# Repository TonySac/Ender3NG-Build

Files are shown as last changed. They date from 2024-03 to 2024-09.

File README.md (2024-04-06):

# The Maker Medic's Ender 3 NG Documentation

Visit my [documentation/log page](https://e3nglog.themakermedic.com).

<b>OR</b>

Check out my main [website](https://themakermedic.com).

<small>

This repo was generated using the [just-the-docs template](https://github.com/just-the-docs/just-the-docs-template).

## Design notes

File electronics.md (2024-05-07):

---
title: Electronics
layout: default
nav_order: 6
has_children: true
posted: 2024-04-17
updated: 2024-04-30
---

# Electronics
{: .no_toc }

<details closed markdown="block">
  <summary>
    Table of contents
  </summary>
  {: .text-delta }
1. TOC
{:toc}
</details>

---

The official documentation does not include information on wiring or installing electronics. The following pages cover the electronics and wiring of my personal E3NG. It should not be considered a standard. It is provided for personal reference and inspiration only.

In addition to the standard printer electronics (steppers, thermistors, & heaters) my build makes use of the following specific components:

* BTT SKR Mini E3 V3 Mainboard
* Raspberry Pi 3A+
* SN65HVD230 CAN Tranciver
* BTT EBB36 CAN Toolhead Board
* LEDs

{: .note }
:pencil2: I later upgraded to a Pi 4 that I had laying around. I ran into some bottlenecks with dev environments on the Pi 3A. The 3A should be fine for just a printer.

# Wiring Guidance

{: .warn }
:warning: Incorrectly wiring components can cause damage and/or personal injury.

Wires should be routed in a clean manner. This means out of the way of motion components and not pinched, kinked, or otherwise damaged. Always use the correct wire gauge. Securely crimp all connections and use electrical tape and/or heat shrink to prevent shorting. Standard color conventions are especially important for power wires. Label wires as needed.

I provided a table below of the wire gauges I used for various components on the build. Remember, the bigger AWG number, the smaller the wire.

| Component | AWG |
|---|---|
| AC Power | 16-18 |
| DC Power | 18 |
| Heaters | 18-20 |
| Thermistors | 22 |
| Fans | 22 |
| Steppers | 22 |
| Bed Probe | 22-24 |
| CANbus Comms. | 22 |

# Main Electronics

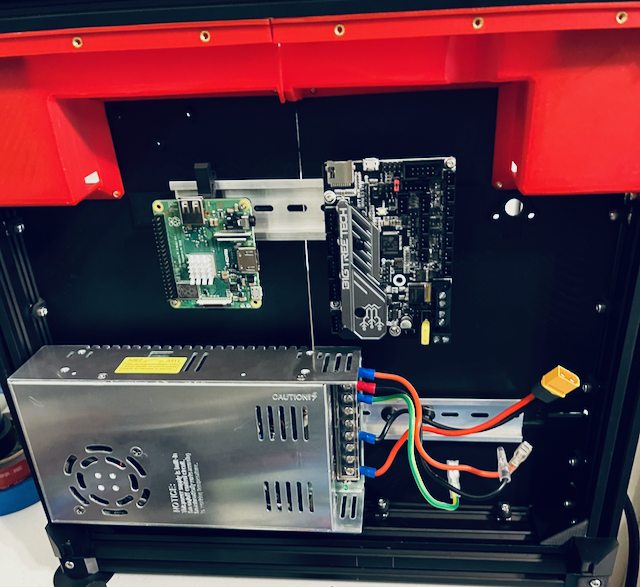
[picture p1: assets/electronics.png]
{: .float-right}{: .ml-3}

I don't feel like there is any "right" way to mount the electronics in the rear of the printer. I used a combination of the included DIN clips and some leftover clips from my Voron build.

The large power supply only fit on the lower DIN rail. I was unsuccessful using `PSU3` and ended up using the standard `DIN1` clip with enlarged holes. In the future I would like to add a buck converter to this lower rail to power the Raspberry Pi. I also need to figure out a more stable way to secure the DIN rail itself.

The upper DIN rail is home to the Raspberry Pi, mainboard, and a CAN transceiver.  I used the DIN clips and brackets from my Voron build, simply because they were already printed and on hand.

For the time being, I do not have an enclosure on the rear of the printer. I would like to clean up the wiring and either print or cut a nice panel to cover the back.

# Toolhead Electronics

{: .mod }
:wrench: Instead of Klicky, I'm reusing the CR Touch.

As previously mentioned, I'm running a Voron Stealthburner for the toolhead. In addition to the usual components (fans, thermistor, and heater) it has some LEDs. I'm also running a BTT EBB36 toolhead board via CANbus. Eventually I will upgrade the CR Touch to a better bed probe and maybe even change the toolhead. 

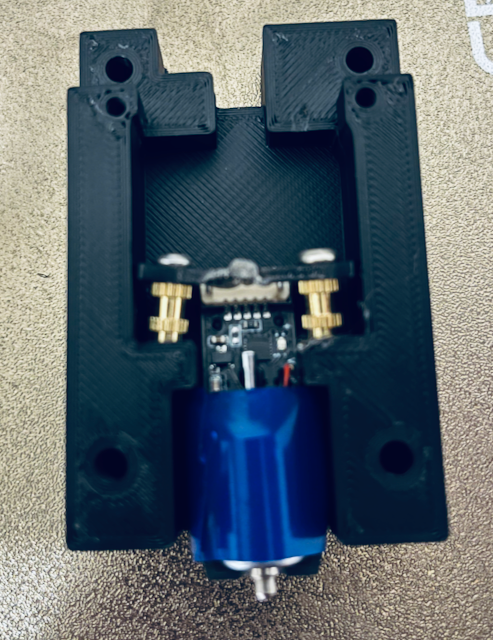
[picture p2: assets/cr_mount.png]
{: .float-right}{: .ml-3}

I made some modification to the CR Touch housing and used [this](https://www.printables.com/model/709806-ender-3-ng-vocano-voron-bltouch-stealthburner) mount to attach the Stealthburner to my E3NG. The mount was originally designed for a BL Touch so I needed to shave down and remove some of the CR Touch housing. I also had to add some spacers to the mount.

>A more elegant solution would be to redesign a mount that fits the probe correctly. With my currently subpar CAD skills and plans to upgrade the probe, I went with my modification instead. 

The big thing to remember with toolhead electronics is to route the wiring an a way that it does not jam up any motion components. The EBB36 CANbus toolhead board helps in this regard. I used one of the many EBB36 mounts found online for the Stealthburner/Clockwork2 then routed and secured loose wires with zip ties.

# Bed Electronics

I reused the stock Ender 3 bed including heater and thermistor. This just required routing the existing cables. Future plans include adding some sort of quick disconnect, maybe WAGOs, to make the bed easier to remove along with a cable chain.

# Switches and LEDs

The Y endstop switch gets mounted on the A motor mount. Originally I planned to use sensorless homing and still will for the X axis. However I had some issues with the calibarating sensorles homing on the Y So I returned to a standard switch. Keeping with the E3NG spirit, I reused an Ender 3 switch and some wiring. I cut the endstop out of the old mounting board and used some DuPont connectors for the pins. For reference, the X endstop is would be secured to the rear of the toolhead carriage and the Z endstop is screwed into the Z motor mount.

The Stealthburner toolhead already has some integrated LEDs. Other than that, I am planning on mounting some in the print area but have yet to map that out.

# LCD Screen

I would like to add a screen. Since I'm using the EXP1 header for CANbus I am still trying to figure this part out.

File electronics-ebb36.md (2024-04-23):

--- 
title: EBB36 Wiring
layout: default
parent: Electronics
nav_order: 2
posted: 2024-04-22
---

# EBB36 v1.2 Toolhead Wiring
{: .no_toc }

<details closed markdown="block">
  <summary>
    Table of contents
  </summary>
  {: .text-delta }
1. TOC
{:toc}
</details>

---

I use BTT's EBB36 Toolhead board. Once again, schematics and pinout can be found on [GitHub](https://github.com/bigtreetech/EBB) and I included a screen shot of the pinout below.

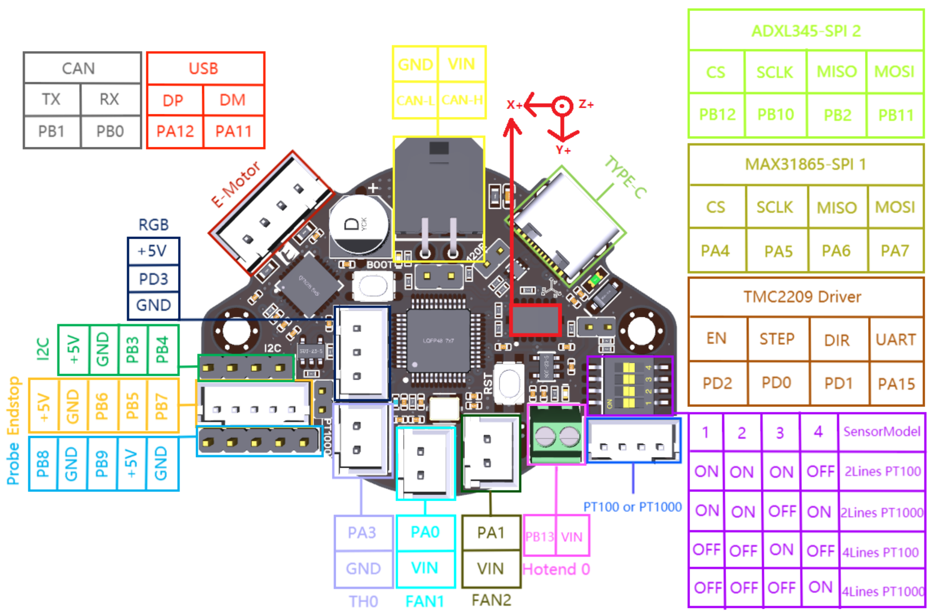
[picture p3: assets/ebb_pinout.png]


Regardless of USB or CAN communication, the EBB36 requires 24v power. I tapped directly off the main power supply and crimped the included 2x2 Molex Mircofit connector. 

{: .warn }
:warning: The pinout diagram can be a bit confusing. When orienting the EBB36 as shown in the diagram, the rear two Molex pins are `GND` and `VIN` respectively. Miswiring the board can send it up in smoke.

## CANbus Wiring

The `CAN-L` and `CAN-H` pins should be wired directly to the `CANH` & `CANL` pins on the CAN tranciever. On the EBB36, these pins can be accessed either via the Molex connector or the two DuPont pins below it.

CANbus wire harness are available from a number of suppliers. The CAN high and CAN low wires should be a twisted pair. The power wires should not be twisted. Since this was a small run, I twisted my own 22 ga wire and secured it intermittently with zip ties then tucked it into a cable loom next to the 18 ga power wires with everything terminating into the 2x2 Molex Microfit connector at the toolhead. 

### Terminating Resistor

The CAN network requires two 120 &#937; resistors, one at each end of the network. My network starts at the CAN tranciever which happens to have a built in terminating resistor. Most of the time the EBB36 will be the last, or only other, node on the network. A jumper must be placed across the `120R` pins to enable the 120 &#937; terminating resistor.

## E Motor

Plug the extruder motor into this connector. Review the information on stepper motor windings in the [previous section](/electronics-wiring.html#stepper-motors).

{: .tip }
:bulb: The EBB36 includes a heatsink that should be placed on the TMC2209 driver. That is the chip just below this connector.

## RGB

Any toolhead LEDs can be plugged in here. Pay attention to the power and communication pins.

## Endstop

I used this connector for the CR touch. The `Probe` header would have been a drop in fit but required a DuPont connection. I preferred a more secure JST fitting. Just remember to order the pins correctly and this header uses JST 1.5. 

## Hotend

The thermistor plugs right into `TH0` and the heater cartridge used ferrules to screw into `Hotend 0`. The polarity is not important for these components.

## Fans

The part cooling and hotend fans plug into the `FAN1` & `FAN2` ports. It doesn't matter which goes where as this can be addressed in firmware.

## Other Pins/Components

I am not using the additional headers at this time or the MAX31865 temperature sensor. Setting up the integrated ADXL will be covered in the [configuration section](/software_configuration.html).

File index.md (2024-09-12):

---
title: Overview
layout: default
nav_order: 1
posted: 2024-03-16
updated: 2024-04-22
---

# The Maker Medic's Ender 3 NG

---

{: .notice} 
:loudspeaker: As of September 2024 I have passed this project along to another member of the E3NG/RH3D community. I will no longer be updating this log. The site will remain active as long as possible for reference.

This documentation logs my Ender 3 NG build. It serves as a log of my process and in some parts an unofficial guide. I did not build this E3NG exactly to spec. It will likely become a project printer that I continue to tinker with. I plan to continue to update these pages as things change and progress. I started the project in March 2024 during a beta release.

> Keep in mind, this is my specific printer. I have attempted to generalize some parts of this documentation but it really is a reference to myself and my process. There are no guarantees this information is 100% correct, up to date, or will even work. I am not responsible for any damage or harm from trying the things outlined in this document.

I've attempted to call out things I found along the build journey using the following highlights:

{: .note}
:pencil2: General Notes

{: .tip}
:bulb: Tips/Tricks 

{: .mod }
:wrench: Modifications

{: .notice}
:loudspeaker: Notices/Alerts

{: .warn }
:warning: Warnings

## Timeline

As of mid April 2024, I was successfully printing on the E3NG. I spent the month of March intermittently printing parts on my Voron 0.2 and the donor Ender 3. Mechanical assembly took roughly 1.5 days and wiring up electronics took another half to full day. Outside of printing and sourcing parts, it took me about 2-3 days to go from boxes of parts to a functional printer.

## Background

The Ender 3 NG is a coreXY conversion for the Ender 3 series of printers. The project was created by RH3D and all information about the Ender 3 NG project can be found on [Printables](https://www.printables.com/model/469280-ender-3-ng-corexy-beta). This includes the official build manual, the bill of materials and sourcing guide, STLs, and more.

After building a Voron 0.2, I initially planned on converting my old Ender 3 Neo into a Voron Switchwire. When I stumbled upon the Ender 3 NG project I decided to change directions. I preferred the coreXY motion system of the Voron 0.2 and wanted a printer I could continue to tinker with.

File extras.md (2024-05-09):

---
title: Extras
layout: default
nav_order: 99
posted: 2024-04-07
updated: 2024-05-09
---

# Extras
{: .no_toc }

<details open markdown="block">
  <summary>
    Table of contents
  </summary>
  {: .text-delta }
1. TOC
{:toc}
</details>

---

This section of the includes some extra things I made for my E3NG and the community.

# Mainsail Theme

I threw together a pretty basic Mainsail theme based around the Ender 3 NG. It includes logos and sidebar images. I'm a fan of the default dark interface so I left most that as is.

The theme can be found on my [GitHub](https://github.com/TonySac/E3NG-Mainsail-Theme). More info on Mainsail themes can be found [here](https://docs.mainsail.xyz/overview/features/themes).

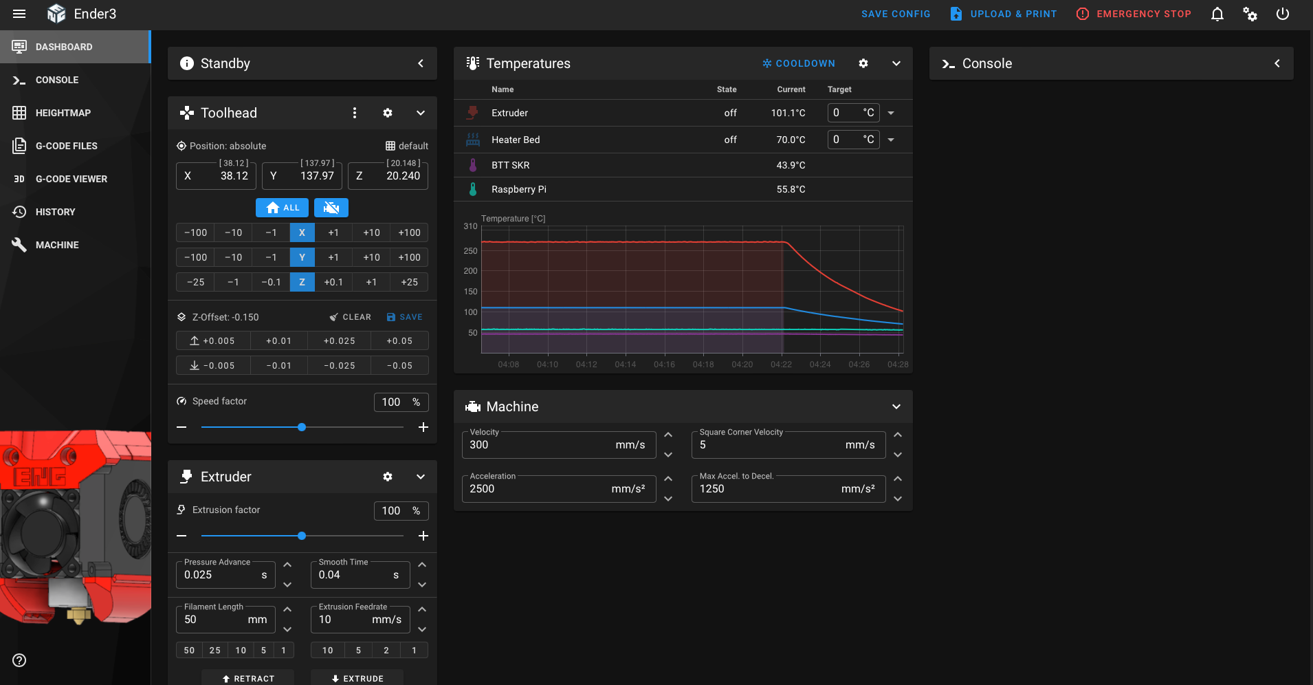
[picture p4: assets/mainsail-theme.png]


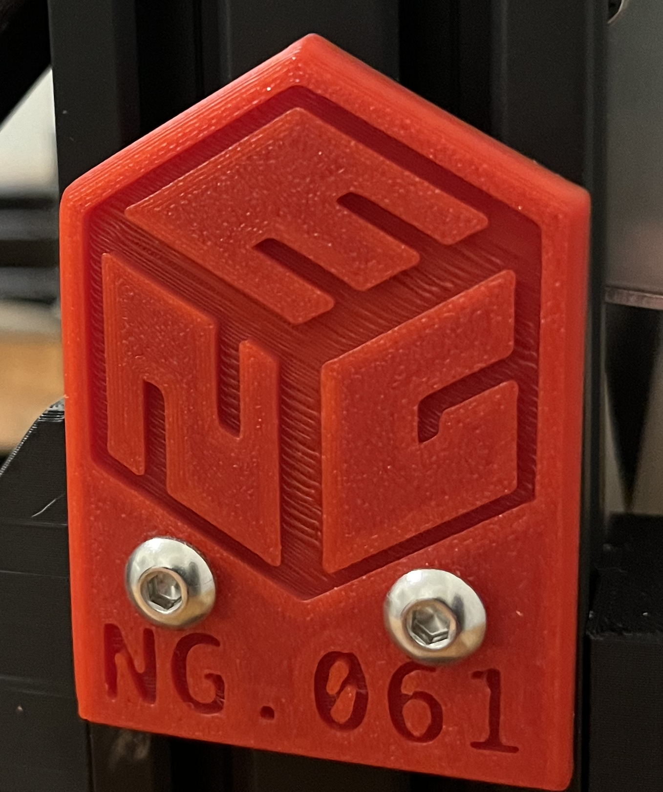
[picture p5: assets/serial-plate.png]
{: .float-right}{: .ml-3}

# Serial Plate

I threw together a simple serial plate for those with serialized E3NGs. I mounted it on the 2040 extrusion mod uprights but it can really go anywhere there is a free extrusion slot. It is still a work in progress. The files are all on [Printables](https://www.printables.com/model/874151-e3ng-serial-plate-for-2040-upright). These include a STEP file without any text and a F3D file for easy editing of the serial number.

<br>

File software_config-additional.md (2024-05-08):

---
title: "Additional Configuration"
layout: default
nav_order: 2
parent: "Software Configuration"
has_children: true
posted: 2024-05-07
---

# Additional Configuration
{: .no_toc }

<details closed markdown="block">
  <summary>
    Table of contents
  </summary>
  {: .text-delta }
1. TOC
{:toc}
</details>

---

This section covers some additional configuration features used on my printer. Although not mandatory for printing, they are quality of life improvements.

# Bed Probe

The whole point of the CR Touch is to create a bed mesh for auto leveling. Klipper also includes a feature to help with adjusting the bed screws.

## Bed Mesh

In order to generate a bed mesh in Klipper, the `[bed_mesh]` configuration must be defined. The example below is for my machine.

```yaml
[bed_mesh]
speed: 300
mesh_min: 0, -9
mesh_max: 223, 190
probe_count: 5,5
algorithm: bicubic
```

{: .note }
:pencil2: The `mesh_min` and `mesh_max` values are where the nozzle is located during the probing process. As such, the probe offset needs to be added into these coordinates and any machine constraints accounted for.

Additionally, I still use [KAMP](https://github.com/kyleisah/Klipper-Adaptive-Meshing-Purging) for generating an adaptive mesh. More recent versions of Klipper have this feature built in but I have not gotten around to transitioning to it.

Don't forget to call or load the bed mesh when a print is started.

## Bed Screws

Rather than fiddling around with paper, `[screws_tilt_adjust]` can be configured. Then `SCREWS_TILT_CALCULATE` called in Mainsail for the probe to calculate the offset of each bed screw and the recommended adjustment. This configuration parameter is defined on my machine as follows:

```yaml
[screws_tilt_adjust]
screw1: 27, 12
screw1_name: Front Left
screw2: 195, 12
screw2_name: Front Right
screw3: 195, 181
screw3_name: Back Right
screw4: 27, 181
screw4_name: Back Left
screw_thread: CW-M4
```

{: .note }
:pencil2: Once again, the coordinates refer to the nozzle location. Adjust them with the probe offset in mind so the probe is directly over each bed screw.

# Input Shaper

Input shaping helps counteract some of the printer's vibrations to imporve print quailty at higher speeds. See the Klipper documentation on [Resonance Compensation](https://www.klipper3d.org/Resonance_Compensation.html) for more information.

It is defined under the `[input_shaper]` configuration parameter. Manual tests can be performed to calculate the associated values. However, I use an accelerometer, specifically and ADXL345 that is integrated on my EBB36 to do all of the work for me.

First the accelerometer needs to be defined in Klipper. The example below are the pin mappings for the integrated EBB36 ADXL and my defined MCU.

```yaml
[adxl345]
cs_pin: EBB36_Toolhead: PB12
spi_software_sclk_pin: EBB36_Toolhead: PB10
spi_software_mosi_pin: EBB36_Toolhead: PB11
spi_software_miso_pin: EBB36_Toolhead: PB2
```

The `[resonance_tester]` must also be configured. The ideal coordinates are just above the center of the print bed.

```yaml
[resonance_tester]
accel_chip: adxl345
probe_points:
    114.5, 117.5, 10
```

Before running any tests, review Klipper's documentation on [Measuring the Resonance](https://www.klipper3d.org/Measuring_Resonances.html#measuring-the-resonances_1) for a better understanding.

Once everything is set up, `SHAPER_CALIBRATE` will automatically run the tests, measure the resonance, and update the input shaper values in Klipper. It will also give a value that can be used to tune for `max_accel`.

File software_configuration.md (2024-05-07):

---
title: "Software Configuration"
layout: default
nav_order: 8
has_children: true
posted: 2024-05-07
---

# Software Configuration
{: .no_toc }

<details closed markdown="block">
  <summary>
    Table of contents
  </summary>
  {: .text-delta }
1. TOC
{:toc}
</details>

---

{: .notice }
:loudspeaker: These steps assume the Klipper host is running and accessible from the local network.

This section covers configuring Klipper for the Ender 3 NG. Specifically, it covers the configuration of a BTT SKR Mini E3 v3 in USB to CAN bridge and a EBB 36 Toolhead board.

The Klipper GitHub contains [configuration examples](https://github.com/Klipper3d/klipper/tree/master/config) for not only these boards but also some generic configs and resources for other control boards. These provide a good starting point for the configuration. Additionally, my [personal Ender 3 NG config files](https://github.com/TonySac/Ender3NG-Config) are hosted on my GitHub.

{: .note }
:pencil2: Neither my config nor the example configs are plug and play. Some validation and updating will be required for any machine.

After experimenting with Klipper on my Ender 3 Neo and building a Voron 0.2, I pulled from those configuration files and the [Klipper Configuration Reference](https://www.klipper3d.org/Config_Reference.html) to generate my own E3NG config.

> My old [Ender 3 Neo config](https://github.com/TonySac/Ender-3-Neo-Config) and current [Voron 0.2 config](https://github.com/TonySac/Voron0-Config) can also be found on my GitHub.

# Editing the Config Files

The Klipper config files are stored on the host system in `~/printer_data/confg`. The files can be accessed from the Mainsail web interface under the `Machine` tab. They can also be edited directly on the host or remotely via SSH and tools like VSCode. A simple `Save & Restart` immediately applies changes to the firmware.

Comments in the config code are superseded with `#`. Additional files can be placed in the `~/printer_data/confg` directory with a *.cfg* extension and included with an `[include additional.cfg]` line in *printer.cfg*. This is useful for larger custom configurations and macro files. When pins are defined special characters can be used. Prepending a pin with `!` inverts the pin polarity. If so equipped `^` enables a hardware pull-up resistor and `~` a hardware pull-down resistor. See some examples below.

```yaml
#This is a comment followed by some examples

[include macros.cfg] #This file is included as if it were part of the config

dir_pin: PB2 #This tells the motor to spin in the default direction
dir_pin: !PB2 #This reverses the motor's default direction

endstop_pin: ^PC1 #This enables the hardware pull-up resistor
```

# Getting Started

The Klipper web interface can be accessed in a web browser using the host's IP address. In this case, I'm using Mainsail.

{: .tip }
:bulb: It's a good idea to set the Klipper host up with a static IP.

Assuming Klipper was properly flashed and and the MCU path updated during [software installation](/software_install.html) the Mainsail interface should load up with a basic screen and no way to control the printer.

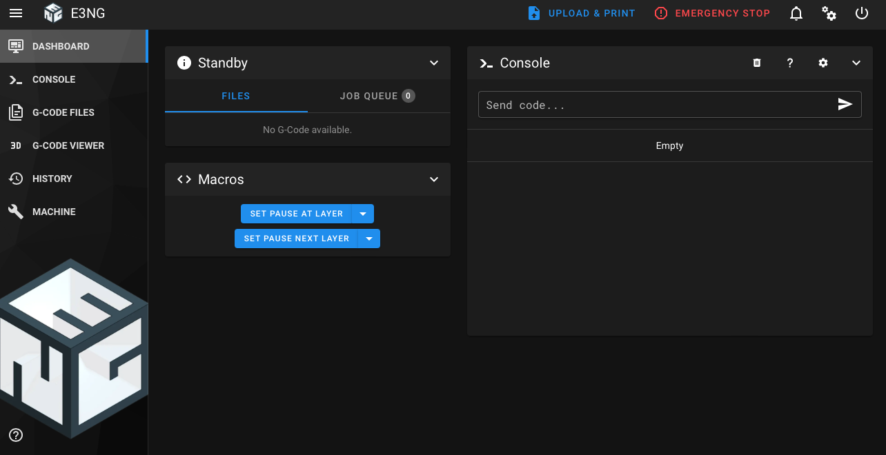
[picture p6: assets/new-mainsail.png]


In the result an error is reported regarding connection to the MCU, it's likely the MCU path is incorrect.

Navigate to `Machine` then `printer.cfg`.

If the printer is connected to the host via USB, the `mcu` line should read:

```yaml
[mcu]
serial: /dev/serial/by-id/usb-Klipper_Klipper_firmware_12345-if00
```

Where the correct `/serial/by-id/` path is found by running `ls /dev/serial/by-id/*` on the host machine.

If USB to CAN bridge mode is used, then the `mcu` line should be similar to

```yaml
[mcu]
canbus_uuid: 027a9447a345
```

The `canbus_uuid` can be found by running `~/klippy-env/bin/python ~/klipper/scripts/canbus_query.py can0` on the host machine.

If the problem persists, troubleshoot the wiring and Klipper installation.

Once the interface is accessible, building the configuration can begin.

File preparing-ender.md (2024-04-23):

--- 
title: "Ender 3 Prep"
layout: default
parent: Preparing Parts
posted: 2024-04-09
updated: 2024-04-22
---

# The *Ender* of an Era
{: .no_toc }

<details closed markdown="block">
  <summary>
    Table of contents
  </summary>
  {: .text-delta }
1. TOC
{:toc}
</details>

---

{: .note }
:pencil: My Ender 3 Neo had the same extrusion sizes as the Ender 3 Pro (the standard conversion printer). It did however have the fatter power supply.

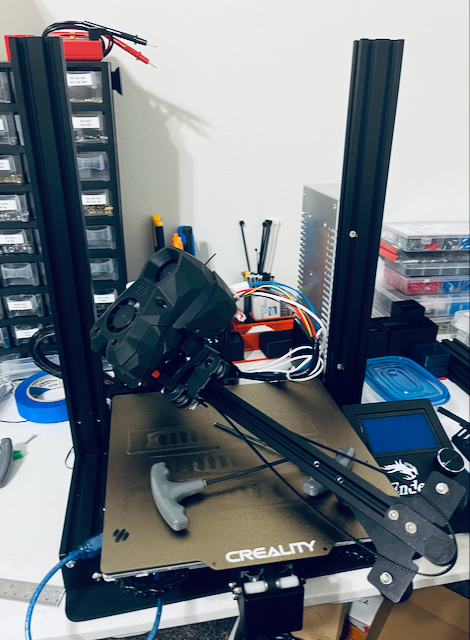
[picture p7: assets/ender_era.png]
{: .float-right}{: .ml-3}

Disassembling the Ender 3 is pretty straight forward. Place the extrusions off to the side. Pull out any electronics that will be reused. Separate the bed plate. The build surface itself can be left intact. Make sure to hold on to anything planning to be upcycled (PEI sheet, leadscrew, nut, etc.). The POM wheels, mounts/brackets, and old belts are basically garbage at this point. I held onto most of the screws, I can usually find a use and the M5 screws came in handy as a cheap thread tap.

# Old X Axis

The old X axis is a 345mm 2020 extrusion. This was the only one on my printer without the ends tapped. I did not have a tap set on hand. With some patience and a little 3 in 1 oil I had laying around I used an old M5 screw to slowly cut threads.

{: .warn }
:warning: Saws cut, drills make holes, and sharp metal hurts.

# Z Screw

I reused the Z screw from the Ender. This required cutting it down to the appropriate length. 300mm is specified in the BOM. I simply lined it up with one of the 300mm leadscrews I purchased and cut it with a hacksaw. The next appropriate step would be to bevel the edge. Instead, I hid it on the bottom side of the printer. Regardless, make sure to clean the leadscrew after cutting it then thread a nut on/off the cut end several times to help clean it up.

{: .tip }
:bulb: The stock Ender 3 leadscrew nut was not a perfect fit for the E3NG upgrade. If reusing the leadscrew, consider still purchasing a new leadscrew nut.

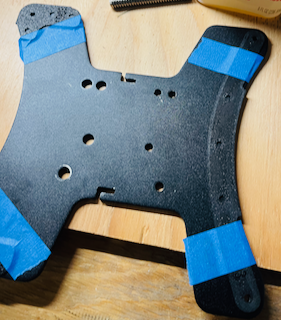
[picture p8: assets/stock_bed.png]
{: .float-right}{: .ml-3}

# Bed Plate

In order to mount the bed plate, it requires some new holes to be drilled. Fortunately, the part files also include templates. After printing those off, I taped them to the bed plate to keep alignment. A little more 3 in 1 oil (real cutting oil would be best) and a drill press made quick work of this. If screwing directly into the bed, the manual states use a 3.5mm drill. For my fellow Americans, a 9/64" bit is 3.57mm... close enough.

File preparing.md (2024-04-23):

---
title: Preparing Parts
layout: default
nav_order: 3
has_children: true
posted: 2024-03-19
updated: 2024-04-22
---

# Preparing Parts
{: .no_toc }

<details closed markdown="block">
  <summary>
    Table of contents
  </summary>
  {: .text-delta }
1. TOC
{:toc}
</details>

---

In order to streamline assembly, I inspected parts as they were received or printed. I then post processed, inventoried, and organized them. I used the BOM as my source of truth for inventory and highlighted the items I had on hand along with any notes I needed to make.

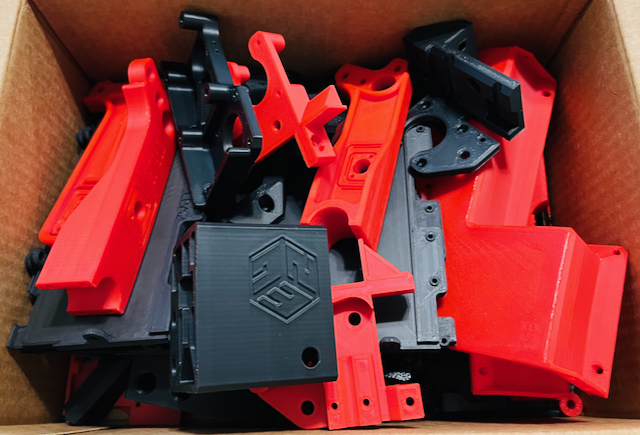
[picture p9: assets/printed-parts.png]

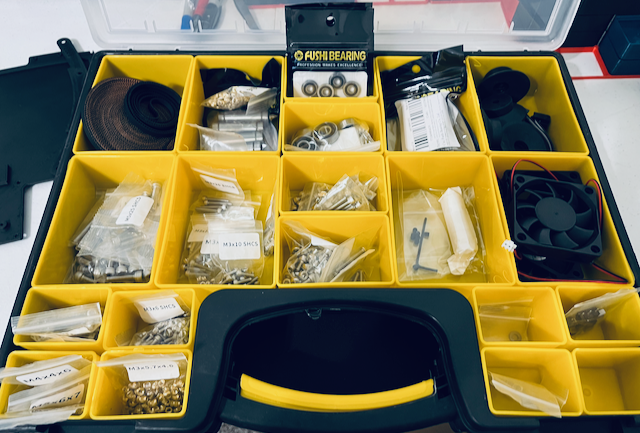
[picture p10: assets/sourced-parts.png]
{: .float-right}

# Inspection and Post Process

As the parts came off the printer, I inspected them for quality. I already confirmed tolerances with the calibration cube prior to producing my parts. At this point, I was looking at the finish and for any unacceptable defects.

{: .warn }
:warning: Be careful with sharp tools and heat sources.

I used a deburring tool and a small pick to remove brims and clean up the edges. I also ran a lighter along the parts to remove discoloration and further smooth things out.
>A heat gun would probably be a better choice.

# Heat Inserts

Once most parts were printed, I went page by page in the build manual and sunk the appropriate heat inserts. By placing all the inserts in advance, I could just pick up and go when it was time to build, rather than pause to place them at each step. I just used a soldering iron with a standard tip to sink these, no special tools.

{: .tip }
:bulb: Use a flat metal surface to push against the insert after it is in place to help it set level and flush to the plastic part.

# Electronics Frame Rims (EF__)

The `electronics frame rims` or `EF__` parts needed to be glued together with `EFJ` for final assembly. I took a second to use some super glue and complete this process after I placed the heat inserts. Once again, this made sure these parts were ready to go when I get to this phase of mechanical assembly. 

{: .mod }
:wrench: I split some of the longer rims so they could be printed on my Voron 0.2. This also meant printing additional `EFJs` and an additional glue joint. I'm considering not using the glue joints on final assembly as each rim has a dedicated mount hole. See [here for more information](/sourcing-printing.html#electronics-frame-rims-ef__).

# Lubricating Bearings

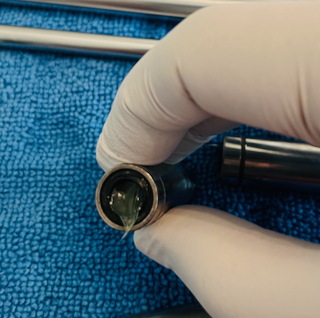
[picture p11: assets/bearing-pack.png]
{: .float-right}{: .ml-3} 

I also batch lubed all of my linear bearings so they would be ready to go when I started building. I used the following method:
   
1. **Clean the Bearings --** 
    I simply soaked them in high percentage (>90%) isopropyl alcohol for a while to clean out any shipping oils and other contaminants. I let them drip and air dry. The IPA evaporates pretty quickly.
1. **Pack the Bearings --**
    I jammed as much grease as I could into the bearings. I used Mobilux EP2 because I had it on hand.
1. **Work in the Grease --**
    Using a clean linear rod, I plugged the open end of the bearing as I slid it on the rod. This pushes as much grease as possible into the bearing races. Move the bearing up and down the rod to work as much grease as possible into the races.
1. **Storage --**
    Once lubricated, I wiped up any excess grease leaving just a thin layer on the outside of the bearing for protection. I cleaned up the linear rod and placed the bearings back in a bag for storage to keep them free of any debris.

# Extrusions

I went with the 2040 extrusion mod, 350mm to be exact. I needed to tap one hole on the bottom of each extrusion to fit an M5 screw for the rubber feet. The appropriate way would be to use a tap set and thread the ends. 

I was lazy and used a little 3 in 1 oil and an old M5 screw. The aluminum is soft enough I could cut 1/2 to 1 full turn before backing out to clear the threads. Take it slow if you go this route.

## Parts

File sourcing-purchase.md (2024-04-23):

---
title: Purchasing Parts
layout: default
nav_order: 1
parent: Sourcing Parts
posted: 2024-03-19
updated: 2024-04-22
---

# Purchasing and Ordering Parts
{: .no_toc }

<details closed markdown="block">
  <summary>
    Table of contents
  </summary>
  {: .text-delta }
1. TOC
{:toc}
</details>

---

After raiding my spare parts drawer, I turned to the BOM and sourcing guide to acquire anything that was missing or I wanted to add.

>The BOM not only contains the recommended parts but also affiliate links. I suggest using these links when purchasing parts in order to help support the project.

{: .tip }
:bulb: Consider lead times when ordering parts and plan the build accordingly.

# Motion

I sourced most of this exactly as specified in the BOM from Aliexpress using the affiliate links. My plans include the 2040 extrusion mod and reusing the Z axis lead screw.

{: .mod }
:wrench: I have upgraded NEMA 17 steppers on my Ender that will carry over.

# Electronics

I already have a BTT SKR Mini E3 V3 in my Ender 3. I added the extended screen cable to my order as I prefer the basic LCD over a touchscreen. I also picked up some DIN rails off Aliexpress. Originally, I considered using the printed DIN cleats from the Voron 0 repo but decided to go with actual rails. I even grabbed an extra to upgrade the Voron.

{: .mod }
:wrench: I plan to use CANbus with a BTT EBB36 CANbus tool head board. I have one in the Voron 0.2 and enjoyed the process of setting it up along with the simplified wiring.

{: .notice }
:loudspeaker: No wiring information is included in the official docs. I had plenty of 16-22 AWG wire and various connectors (JST, Molex, ferrules, etc.) in my spare parts for any needs.

# Hotend

{: .mod }
:wrench: My Ender is already equipped with [Voron Stealthburner](https://vorondesign.com/voron_stealthburner) from my planned Switchwire conversion.

# Hardware

Once again, my parts drawer is full of miscellaneous hardware. However, I lacked most of the socket head screws. I elected to go with an unofficial hardware kit to get started. It contained most of the required parts. Anything remaining I either had laying around or sourced locally. 

# Enclosure

I downloaded the STEP file for information on the enclosure. Once I complete the build, I will revisit enclosing the unit.

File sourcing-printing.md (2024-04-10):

---
title: Printing Parts
layout: default
nav_order: 2
parent: Sourcing Parts
posted: 2024-03-19
updated: 2024-04-10
---

# Printing Parts
{: .no_toc }

<details closed markdown="block">
  <summary>
    Table of contents
  </summary>
  {: .text-delta }
1. TOC
{:toc}
</details>

---

I printed most of my parts on my Voron 0.2. However, with only a 120 x 120 build volume I could only print one part at a time. I had to turn to the ole Ender for some of the larger parts.

{: .tip }
:bulb: Make sure to print everything prior to tearing down your only working printer.

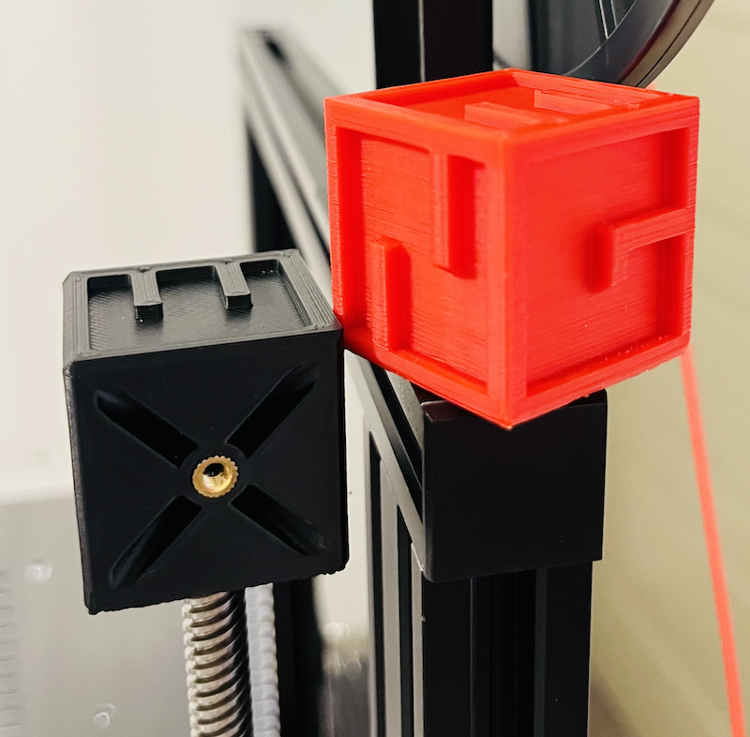
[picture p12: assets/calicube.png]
{: .float-right}{: .ml-3}

A [special calibration cube](https://www.printables.com/model/478403-ender-3-ng-corexy-teasertest-cube) is included with the project. I printed one off on both my Voron and Ender 3 prior to printing the functional parts. Along with a visual inspection, I used the 8mm threaded rod on my Ender 3 and some spare heat set inserts to check my tolerances.

# Materials

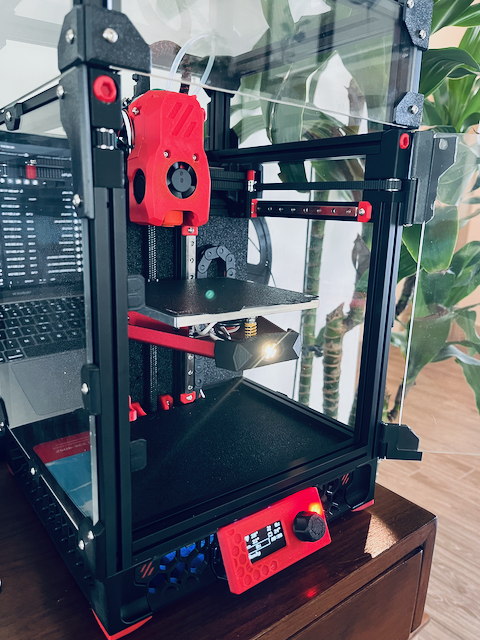
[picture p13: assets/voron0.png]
{: .float-left}{: .mr-3}

I chose to print all of my parts in ABS. ABS is one of the recommended materials and is the Voron standard. I was pleased with the ABS parts I received for my Voron build and I figured I would continue to use it.

Specifically, I used *Sunlu Black ABS* and *Inland Black ABS* for the main parts and *Fusion Filaments Seismic Red ABS 1.5* for the accent parts. I also picked up a spool of *eSun Black ABS+*. Allegedly ABS+ is a bit easier to print with and I will be using it to print the large electronics panels on my Ender. 

# Print Settings

I made some slight modifications to the suggested print settings. Below is a comparison of the E3NG settings and mine:

| |E3NG Settings | My Settings |
|---|---|---|
Layer Height:      | 0.20 mm           | 0.20 mm       |
Infill:            | 30%               | 40% (Cubic)   |
Walls:             | 4                 | 4             |
Top/Bottom Layers: | 5                 | 5             |
Extrusion Width:   | Not specified     | 0.40 mm       |
Supports:          | :x:               | :x:           |
Brim:              | Not specified     | As needed     |

All of the parts were sliced in [OrcaSlicer](https://github.com/SoftFever/OrcaSlicer). My printers and filaments were tuned in accordance to [Ellis' guide](https://ellis3dp.com/Print-Tuning-Guide/).

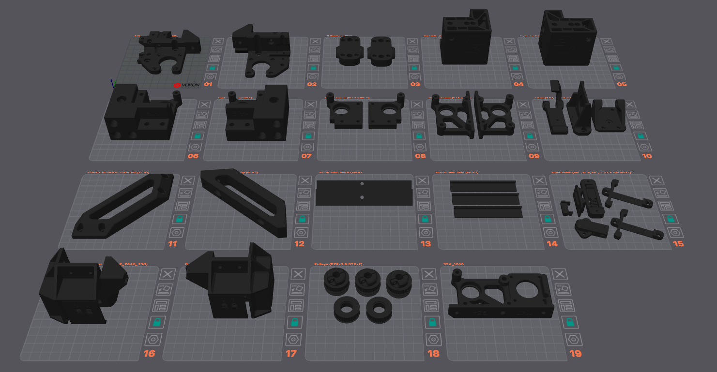
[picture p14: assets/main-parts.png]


For reference, the below 3MF files include the printer, filament, and process settings used on my Voron 0.2. They should load into OrcaSlicer with all of the same settings I used.

* [Voron 0.2 Main Part Project File](https://github.com/TonySac/Ender3NG-Build/blob/main/Orca/E3NG_Main_Parts-Voron.3mf)
* [Voron 0.2 Accent Part Project File](https://github.com/TonySac/Ender3NG-Build/blob/main/Orca/E3NG_Accent_Parts-Voron.3mf)

## Printing ABS on the Ender

For the parts unable to fit in the Voron 0.2, I used my Ender 3 Neo.

Full disclosure, my Ender 3 Neo is not stock. Some of the notable changes are:

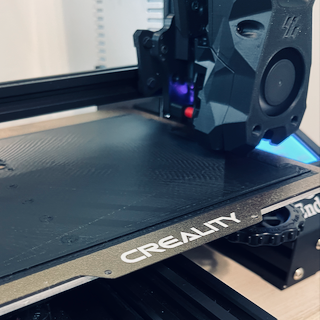
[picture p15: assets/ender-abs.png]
{: .float-right}{: .ml-3}

* BTT SKR Mini E3 V3 Mainboard
* Klipper Firmware
    * Input Shaping
* Upgraded NEMA 17 Steppers
* Stealthbuner Toolhead (Currently reduced build volume)
    * Clockwork 2 Direct Drive Extruder
    * Phaetus Dragonfly BMO Hotend
* Textured PEI Plate

Once again, I included the 3MF files for the parts printed on my Ender 3. 

* [Ender 3 Main Part Project File](https://github.com/TonySac/Ender3NG-Build/blob/main/Orca/E3NG_Main_Parts-Ender.3mf)
* [Ender 3 Accent Part Project File](https://github.com/TonySac/Ender3NG-Build/blob/main/Orca/E3NG_Accent_Parts-Ender.3mf)

I managed to print these parts without an enclosure using *Fusion Filaments Seismic Red ABS* for the stepper motor covers and *eSun Black ABS+* for the electronics panels. I used a brim and hairspray to assist with bed adhesion. The stepper covers had some mild warping but I do not foresee any issues. The electronics panels printed great, other than not noticing the the E3NG logo inlay :frowning_face:. I guess I'll add those to my reprinting list.

# Electronics Frame Rims (EF__)

{: .mod }
:wrench: The following covers a modification I made to an STL.

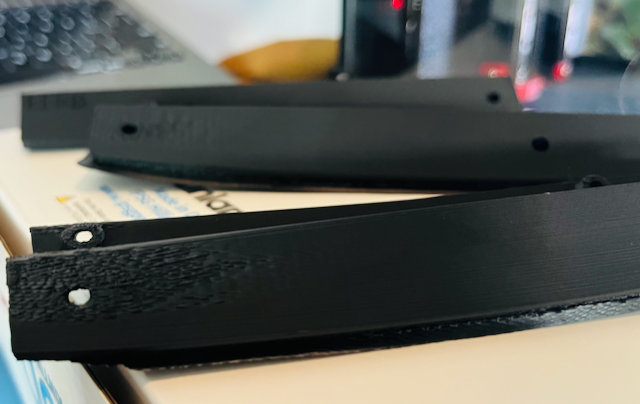
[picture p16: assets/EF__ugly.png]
{: .float-right}{: .ml-3}

I initially printed the `electronics frame rims` on the Ender 3 with *eSun ABS+* and they came out with terrible warps and tolerance issues. 

After reviewing the build manual and STEP file, I noticed these parts are already two pieces that are glued together using the `Frame Joint (EFJ)`. I decided I should be able to split the parts between the mounting holes and reconnect them using additional `EFJs`. I printed off some extra `EFJs` and split the rims in OrcaSlicer. The parts printed without issues on my Voron and seemed to mate just fine.

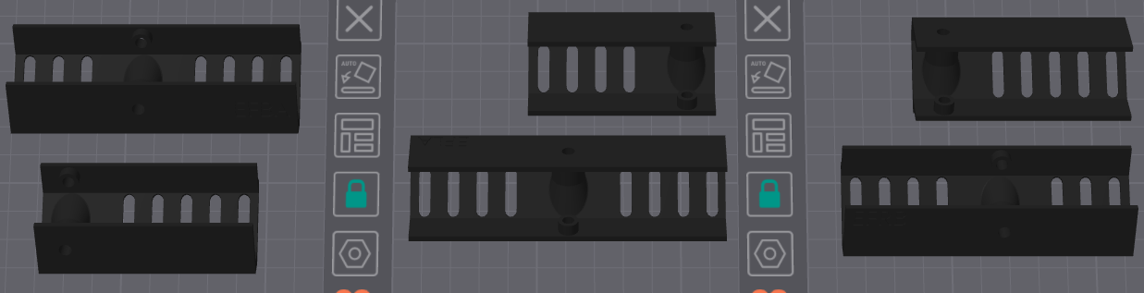
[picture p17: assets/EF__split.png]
{: .ml-3}

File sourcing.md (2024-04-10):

---
title: Sourcing Parts
layout: default
nav_order: 2
has_children: true
posted: 2024-03-19
updated: 2024-04-07
---

# Sourcing Parts
{: .no_toc }

<details closed markdown="block">
  <summary>
    Table of contents
  </summary>
  {: .text-delta }
1. TOC
{:toc}
</details>

---

This build recycles most of the frame and electronics from the Ender 3. However some new motion components are required such as the linear rods and bearings. Additional fasteners are also needed and the new structural components must be 3D printed.

As of this writing, there are no official parts kits (printed or otherwise). All of the required parts, STLs, and sourcing recommendations are on [Printables](https://www.printables.com/model/469280-ender-3-ng-corexy-beta).

# Tools and Consumables

Depending on your tool collection and how in depth this build goes, some additional things will be nice to have on hand that may have not been specified in the BOM.

So far, I have made use of the following tools:

* Decent (metric) allen keys
* Small screwdrivers
* Needle nose pliers and/or tweezers
* Wire cutters & strippers
* Assorted crimping tools (pin, terminal, ferrule)
* Deburring tool & pick set
* Lighter/heat gun
* Soldering iron
* Drill and bits

The same goes for these consumables:

* Grease (Mobilux EP2)
* CA (super) glue
* Zip ties
* Heat shrink
* Isopropyl alcohol
* Cutting oil 

Fortunately, I had most of these things left over from previous projects.

# Cost Breakdown

I put together a small breakdown to help me keep track of costs and help justify expenses. I mean if I already owned the part... it was technically free, right?

| Category | BOM Estimate | My Cost |
|---|---|---|
| Motion | $163.51 | $114.87  | 
| Electronics | $42.64 | $20.44 | 
| Boards | $44.48 | $13.95 |
| Hotend | $43.97 | -- |
| Hardware | -- | $40 |
| Filament | -- | $60.93 |
| **TOTALS** | **$294.60** | **$250.19**  |

<small>Prices in USD</small>

Not all costs were accounted for but this gives a rough estimate. Assuming and Ender style printer is already on hand, I expect most people can complete this conversion for less than $300 USD in parts.

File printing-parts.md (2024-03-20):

---
title: Printing Parts
layout: default
nav_order: 2
parent: Sourcing Parts
---

# Printing Parts

I printed most of my parts on my Voron 0.2. However, since the build volume is so small, some of the larger parts didn't fit. I used my Ender 3 Neo to crank out some of the larger parts.

{: .alert }
Make sure to print everything prior to tearing down your only working printer.

A specialized calibration cube is included in the project files to confirm tolerances. I printed one off on both my Voron and Ender 3 prior to printing the functional parts.

## Materials


{: .float-right}

I chose to print all of my parts in ABS. ABS along with ASA are the recommended materials. I didn't have any experience with ASA. I was pleased with the ABS parts I received for my previous Voron build and I figured if ABS is good enough for Voron, it will be good enough here.

Specifically, I used *Sunlu Black ABS* for the majority of the primary parts and *Fusion Filaments Seismic Red ABS 1.5* for the accent parts. These are the same colors and filaments used on my Voron 0.2 and I wanted to keep with the color scheme.

## Print Settings

I made some slight modifications to the suggested print settings. Below is a comparison of the E3NG settings and mine:

| |E3NG Settings | My Settings |
|---|---|---|
Layer Height:      | 0.20 mm           | 0.20 mm       |
Infill:            | 30%               | 40% (Cubic)   |
Walls:             | 4                 | 4             |
Top/Bottom Layers: | 5                 | 5             |
Extrusion Width:   | Not specified     | 0.40 mm       |
Supports:          | :x:               | :x:           |
Brim:              | Not specified     | As needed     |

All of the parts were sliced in [OrcaSlicer](https://github.com/SoftFever/OrcaSlicer). My printers and filaments were tuned in accordance to [Ellis' guide](https://ellis3dp.com/Print-Tuning-Guide/).



For reference, the below 3MF files include the printer, filament, and process settings used on my Voron 0.2.

* [Voron 0.2 Main Part Project File](https://github.com/TonySac/Ender3NG-Build/blob/main/Orca/E3NG_Main_Parts-Voron.3mf)
* [Voron 0.2 Accent Part Project File](https://github.com/TonySac/Ender3NG-Build/blob/main/Orca/E3NG_Accent_Parts-Voron.3mf)

### Printing ABS on the Ender

For the parts unable to fit in the Voron 0.2, I used my Ender 3 Neo.

Full disclosure, my Ender 3 Neo is not stock. Some of the notable changes are:

* BTT SKR Mini E3 V3 Mainboard
* Klipper Firmware
    * Input Shaping
* Upgraded NEMA 17 Steppers
* Stealthbuner Toolhead
    * Clockwork 2 Direct Drive Extruder
    * Phaetus Dragonfly BMO Hotend
* Textured PEI Plate

Below are the 3MF files the include the settings used on my Ender 3. 

* [Ender 3 Main Part Project File]()
* [Ender 3 Accent Part Project File](https://github.com/TonySac/Ender3NG-Build/blob/main/Orca/E3NG_Accent_Parts-Ender.3mf)

I managed to print these parts without an enclosure. Hairspray and a brim was used to aid with bed adhesion. I did have some mild warping of larger electronics panel parts. I don't foresee this causing issues during assembly as they do not appear to be structural in nature. I will likely reprint them down the road.

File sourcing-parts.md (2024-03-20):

---
title: Sourcing Parts
layout: default
nav_order: 2
has_children: true
---

# Sourcing Parts

This build recycles most of the frame and electronics from the Ender 3. However some new motion components are required such as the linear rods and bearings. Additional fasteners are also needed and the new structural components must be 3D printed.

Currently, there is no *Print it Forward* program. Nor are there any official kits for this build, at least not yet. All of the required parts, STLs, and sourcing recommendations are on [Printables](https://www.printables.com/model/469280-ender-3-ng-corexy-beta).

## Tools and Miscellaneous Items

Depending on your tool collection and how in depth this build goes, some additional things will be nice to have on hand that may have not been specified in the BOM.

I made use of the following tools during the build:

* Decent (metric) allen keys
* Small screwdrivers
* Needle nose pliers and/or tweezers
* Wire cutters & strippers
* Assorted crimping tools (pin, terminal, ferrule)
* Tap set
* Magnet
* Syringes
* Deburring tool
* Lighter
* Soldering iron

The same goes for these consumables:

* Grease (Mobilux EP2)
* Blue Loctite
* CA (super) glue
* Zip ties
* Heat shrink

Fortunately, I had most of these things left over from previous projects. 

## Cost Breakdown

I put together a small breakdown to help me keep track of costs and help justify expenses. I mean if I already owned the part... it was technically free, right?

| Category | BOM Estimate | My Cost |
|---|---|---|
| Motion | $163.51 | $114.87  | 
| Electronics | $42.64 | $20.44 | 
| Boards | $44.48 | $13.95 |
| Hotend | $43.97 | -- |
| Hardware | -- | $40 |
| Filament | -- | $60.93 |
| **TOTALS** | **$294.60** | **$250.19**  |

<small>Prices in USD</small>

Not all costs were accounted for but this gives a rough estimate. I discuss some of these categories in more detail on the following pages.

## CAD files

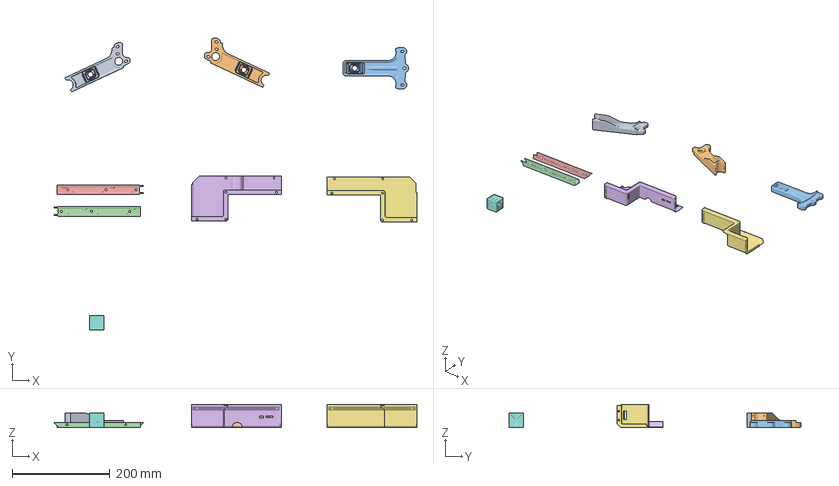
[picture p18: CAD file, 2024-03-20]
Orca/E3NG_Accent_Parts-Ender.3mf
741.2 x 596.1 x 47.4 mm
eng-zca_m_b.stl
eng-zcb_m_b.stl
eng-zcc_m_b.stl
ENG-EMA_b.stl
ENG-EMB_b.stl
ENG-ESA_b.stl
ENG-ESB_b.stl
E3NG-cubeV2.stl

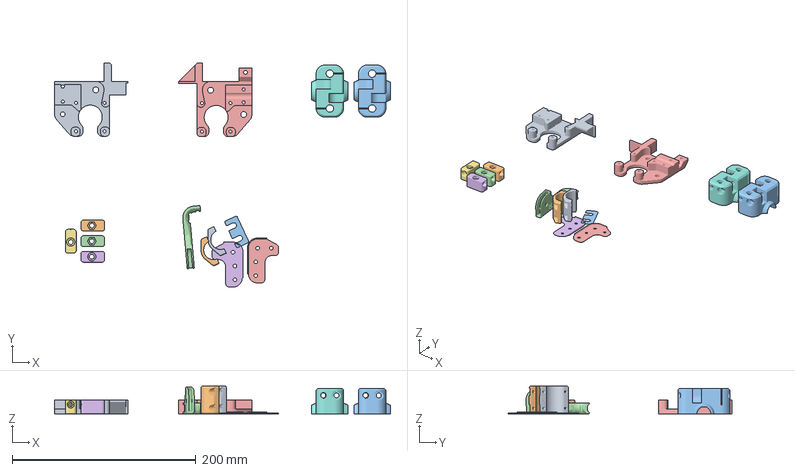
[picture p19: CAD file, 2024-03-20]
Orca/E3NG_Accent_Parts-Voron.3mf
366.1 x 244.3 x 30.0 mm
ENG-MA2_b.stl
ENG-BT2_b.stl x 2
ENG-YGA_b.stl x 2
ENG-MB3_b.stl
ENG-BT1_b.stl x 2
ENG-ZCL_b.stl x 2
ENG-ZCS1_b.stl
eng-bcs_b.stl
eng-bdg1_b.stl
eng-bdg2_b.stl

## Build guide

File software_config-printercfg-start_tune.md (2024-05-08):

---
title: "Startup Tuning"
layout: default
nav_order: 2
parent: "The printer.cfg File"
grand_parent: "Software Configuration"
posted: 2024-05-07
---

# Startup Checks and Tuning
{: .no_toc}

<details closed markdown="block">
  <summary>
  Table of Contents
  </summary>
  {: .text-delta }
1. TOC
{:toc}
</details>

---

Since the E3NG is a newer design, this is a scratch configuration build, and a new firmware install, some basic startup checks and minor tuning is required. These checks make sure the motors and endstops function appropriately, the print area is correctly defined, and the heaters work as expected.

{: .warn }
:warning: All of these checks and steps should be performed with the axis well out of the way of each other and an emergency stop/shutdown procedure ready, available, and working. If the printer fails one of these checks it can result in damage.

# Motion System

The motion system checks first verify the operation of all axis motors and endstops then is followed by tuning of the print area and homing fucntions.

## Verifying Steppers

Start by checking each stepper with the `STEPPER_BUZZ` command. With the bed/nozzle well out of the way use the Kipper console to run: 

```yaml
STEPPER_BUZZ STEPPER=stepper_x
```

This should rotate the `A` motor 1mm clockwise then back 1mm counterclockwise for a total of 10 times. If the desired behavior is not observed verify the `enable_pin`, `step_pin`, `dir_pin`, and `rotation_distance` config settings. Also double check the physical motor connections and locations.

Repeat these checks for `stepper_y` and `stepper_z`

## Verify Physical Endstops

Start by making sure no endstops are depressed. Then run `QUERY_ENDSTOPS` in the Klipper terminal. If everything is correct, you should see the following output:

```yaml
x:open y:open z:open
```

Now manually depress an endstop and run `QUERY_ENDSTOP` again. This time the depressed endstop should report `TRIGGERED`. Repeat this for all physical endstop switches.

> In the event the opposite behavior occurs, invert the pin definition by adding or removing a prepended `!`. If the wrong endstop reports and/or nothing happens verify the wiring, pin assignments, and pullup resistor settings. The pullup resistor is indicated with `^` prepended to the pin name.

Once the physical endstops are verified, we can check the motors home and move correctly.

## Homing Checks

{: .warn }
:warning: Be prepared to quickly stop the printer if the axis is moving in the wrong direction.

### Physical Endstops

Send a home command for a single axis that is equipped with a physical endstop. For the sake of example and because this is about my config. I will use the Y axis. A home Y command `G28 Y` will begin to home the Y axis. The expected behavior is the Y axis moves back until it triggers the endstop, completes a second homing move, then reports a location of about Y 235.

> Based on the `stepper_y` config, the endstop is located at 235mm (which is also `position_max`) so this axis wants to home in the positive direction.

In the event the Y axis moves in the opposite direction, **IMMEDIATELY STOP** the printer. Evaluate the `dir_pin` as it may need to be inverted with `!`. If the X axis moves instead of the Y **IMMEDIATELY STOP** the printer. The A/B cables likely need to be swapped or the pins can be changed in the config file.

Repeat this for any axis with a physical endstop.

### Tune Sensorless Homing

Sensorless homing needs to be tuned and motor direction confirmed for the equipped axis. As long as the max StallGaurd or `driver_SGTHRS` was set in the config it is safe to begin this. Since I'm only using sensorless homing on the X axis, I will be using that example.

Start by attempting to home the X axis `G28 X`. The X axis should begin to move in the positive direction but almost immediately stop. If it does not stop or the wrong axis moves, **IMMEDIATELY STOP** the printer. If the axis moves in the wrong direction, verify the `dir_pin` and invert it with `!` if needed. Take time to double check the motor plugs and other pins as needed.

> Per the `stepper_x` config above, Klipper expects to home in the positive direction, this can be changed per preference.

If everything is moving properly, manually lower the StallGaurd threshold using `SET_TMC_FIELD FIELD=SGTHRS STEPPER=stepper_x VALUE=###`. Where `VALUE=###` is max at 255 and min at 0. Manually lower this threshold and continue to attempt to home the axis until it successfully homes without banging into the rail. Record the max StallGaurd that successfully homes the axis. My StallGaurd_Max was 90.

Continue to lower the StallGaurd value until the axis homes with a noticeable bang or skipped step. Increase the value +1 and confirm the axis homes without issue. Record this value as the minium StallGaurd for a successful home. On my printer StallGaurd 58 resulted in a bang but StallGaurd 59 homed fine. Therefore, my StallGaurd_Min was 59.

Use the following formula to calculate the new `driver_SGTHRS` value:

```
driver_SGTHRS = [(StallGaurd_Max - StallGaurd_Min)/3] + StallGaurd_Min
```

Example:

```
[(90-59)/3]+59 = 69.33 =~ 70 {I opted to round up}
```

Update `printer.cfg` and repeat the process as needed.

{: .notice }
:loudspeaker: If changes are made to the printer hardware or motor configuration, including belt tensions, motor currents, speeds, etc. then sensorless homing may require additional tuning.

### Z Endstop/Probe

Since this build is equipped with a CR Touch, it will be used as the Z endstop. If installed and wired correctly, the CR touch should self test on startup then have a steady blue LED. Confirm the probe functionality with `BLTOUCH_DEBUG COMMAND=pin_down` to lower the probe pin, followed by `BLTOUCH_DEBUG COMMAND=pin_up` to raise the pin. 

Check the sensor by lowering the pin `BLTOUCH_DEBUG COMMAND=pin_down` and entering touch mode with `BLTOUCH_DEBUG COMMAND=touch_mode`. Run `QUERY_PROBE` and verify the output os `open`. Gently push the pin and `QUERY_PROBE` the result should now show `TRIGGERED`.

If these tests fail, verify the probe wiring and double check the configuration definitions.

It goes without saying the probe should also be slightly above the nozzle with it is stowed. Additionally, take the time now to measure the distance between the probe and nozzle. Update the config with the correct `x_offest` and `y_offset` as needed. Remember these can be negative values.

Once the probe functions as expected, center the print bed and prepare to test the Z homing. Run `G28 Z`. The expected behaviro is hte probe will deploy then the bed will begin moving upwards towards the probe. If this does not happen, **IMMEDATLY STOP** the printer.

  > If the probe failed to deploy, check the wiring, config, and rerun the above tests. If the bed moves in the wrong direction, check the `dir_pin` in `[stepper_z].

As the bed is moving towards the probe, manually trigger the probe to confirm the bed stops. **IMMEDIATELY STOP** the printer if the bed does not stop. 

If the manually triggered probe stopped the bed, it is time to run real Z home test. Assuming the X/Y endstops have also been configured, this can be done alongside a complete machine home. Before this is done, it is important to add a `[safe_z_home]` section to the config. This tells the machine how to position the toolhead prior to homing. A good starting point is as follows:

```yaml
[safe_z_home]
home_xy_position: 117.5, 117.5 
z_hop: 10                
```

This will move the bed 10 mm out of the way prior to homing, then position the toolhead at the specified position before homing the Z axis. The `home_xy_position` value should be calibrated to the true center of the print bed.

If the process is successful, allow the Z axis to run a homing routine with the probe actually touching the bed.

## X/Y Motion Range

The motion range can be defined in Klipper by using a combination of the `postion_min`, `position_max`, and `position_endstop` values in the stepper motor configurations. Defining these values prevents the printer from making a move out of range or a crash from occurring.

For the sake of this example, I will be using the Y axis. The procedure is the same for X.

{: .warn }
:warning: The `position_min` value will need to be made negative for this procedure. This increases the possibility of a toolhead crash and machine damage. Use caution. 

Start by setting the `postion_min` to a negative number. -25 is usually sufficient. With this complete, home the Y axis. Since my build homes towards the maximum travel, I will record the reported value as Y_Max. Slowly step the axis over until the nozzle is directly over the maximum point (or back) of the bed and record this value as Y_Bed_Max. Continue to step the axis until it is just over the minimum point (or front) of the bed and record this as Y_Bed_Min. Finally, continue to move the axis until it can no longer physically move and record this as Y_Min. 

We want Klipper to use the front of the bed as the 0 or origin point for the Y axis. Use the following formulas to update *printer.cfg*. Pay close attention to any negative values.

```
position_max = Y_Max -  Y_Bed_Min 
position_min = Y_Min -  Y_Bed_Min 
position_endstop = position_max
```

> The difference between Y_Max and Y_Min `(Y_Max - Y_Min)` can be used to determine the true print volume.

Input these changes and home the axis. Verify the printer reports the location of 0 when the nozzle is just over the front of the bed. Then verify the carriage cannot move beyond the set limits or bump the rails.

Repeat this as needed for the X axis. Be sure to input the print volume and origin location into the slicer.

> I'm using a Stealthburner toolhead. This limits some of the printable area. Rather than lose about 35 mm off the Y axis, I took about 10 mm off the X axis (5 on each side). This means the origin point is just to the right of the bed edge on my build. It also means I can still crash my toolhead on the front right frame if I'm not careful. Most of this can be addressed in the slicer and with some macros.

## Z Motion Range

With the use of the CR touch, I usually just leave this set to the theoretical maximum. Unless I plan to print parts that are close to the Z limit. I do recommend changing the `position_min` to around -2 to -5 to facilitate later tuning of the Z offset.

# Extruder Checks

## Fans

Before checking the extruder heater, make sure the fans work. The Mainsail fan control should have the part cooling fan controllable on the front end. Increase its speed to 100% and make sure it is indeed the part cooling fan that turns on. In the event the hotend fan turns on, simply update the pin definitions in *printer.cfg*. If nothing happens, then verify both the wiring and pin definitions are correct.

## Heater

Next, check the extruder heats up. Set the extruder temp to 200&deg;C. The expected behavior is for the hotend fan to engage and the extruder to start to heat. Return the extruder temp to 0&deg;C. The extruder should begin to cool and the fan will turn off once below the minimum set temperature.

## Motor

Finally, make sure the extruder motor is working as expected. On a direct drive, this is often easier to do at temperature and with filament loaded. Heat the extruder to the appropriate extrude temperature and run an extrude command. The motor should turn in the correct direction. If not, verify the pins and connections.

{: .note }
:pencil2: If so inclined, e steps can also be calibrated at this time.

# Verify Heated Bed

Similar to the extruder, check the heated bed. Set the bed temp to 50&deg;C. The bed should slowly start to heat up. Return the bed temp to 0&deg;C and it should begin to cool down.

# PID Tune

Although not immediately required, it is helpful to tune the PID controller prior to attempting a print. This avoids heater out of range errors. Make sure to set the printer up and tune for as close to normal printing conditions as possible.

Run `PID_CALIBRATE HEATER=heater_bed TARGET=##` to calibrate the bed. Where `TARGET=##` should be the bed temperature planned to be used. Once this is complete save the values and run it again but this time for `HEATER=extruder` along with the appropriate temperature. I also recommend setting the print fan to the expected speed for this calibration.

---

# Time to Print!

With the *printer.cfg* file completed and some startup checks/tuning done it is time to run a first print. A Benchy or Calibration Cube are always good choices. These will also help with identifying any remaining issues. For perfect prints, additional calibration will still be needed. I recommend [Ellis' Guide](https://ellis3dp.com/Print-Tuning-Guide/) along with [Teaching Tech](https://teachingtechyt.github.io/calibration.html) and some of [OrcaSlicer's built in calibration tools](https://github.com/SoftFever/OrcaSlicer/wiki/Calibration).

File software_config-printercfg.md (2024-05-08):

---
title: "The printer.cfg File"
layout: default
nav_order: 1
parent: "Software Configuration"
has_children: true
posted: 2024-05-07
---

# The *printer.cfg* File
{: .no_toc }
---

I chose to generate my own initial configuration from previous knowledge while also referring to my other printers and [Klipper's configuration reference](https://www.klipper3d.org/Config_Reference.html).

This document covers the step by step generation of my *printer.cfg* file.

{: .note }
:pencil2: I found it easier to do some of the startup checks/tuning as the configuration was generated. For brevity of this document, I broke them out into a [Startup Tuning](/software_config-printercfg-start_tune.html) sub document and linked out as needed.

My configuration is broken down as follows:

<details open markdown="block">
  <summary>
  printer.cfg
  </summary>
  {: .text-delta }
1. TOC
{:toc}
</details>
---

{: .notice }
:loudspeaker: Remember this is all specific to my particular machine. All pin definitions should be verified and changes made in accordance with the hardware in use.

A fresh Klipper & Mainsail installation should have generated a bare bones *printer.cfg* file.

```yaml
[include mainsail.cfg]
[mcu]
serial: /dev/serial/by-id/<your-mcu-id>

[virtual_sdcard]
path: /home/E3NG/printer_data/gcodes
on_error_gcode: CANCEL_PRINT

[printer]
kinematics: none
max_velocity: 1000
max_accel: 1000
```

Make sure to keep the `[include mainsail.cfg]` and the information in the `[printer]` section. The entire `[virtual_sdcard]` section can be removed as it is duplicated in *mainsail.cfg*. 

# MCU Settings & Features

As the title suggests, this block holds the MCU definitions and enables Klipper features.

My primary mcu communicates via USB to CAN bridge and is defined with the following code. The `canbus_uuid` is unique per machine.

```yaml
[mcu]
canbus_uuid: 027a94e7a31e
```

I also added a temperature reading to the frontend for this board by using the `[temperature_sensor]` option. Where "SKR" is my chosen name for the controller.

```yaml
[temperature_sensor SKR]
sensor_type: temperature_mcu
min_temp: 0
max_temp: 100
```

The EBB36 CAN toolhead board was then added to the configuration.

```yaml
[mcu EBB36_Toolhead]
canbus_uuid: cf152fa74cfc
```

> Since this is an additional mcu, I gave it the name `EBB36_Toolhead`. This will be referred to in later sections.

Once again, I added a temperature sensor to the fronted. This time I needed to define `sensor_mcu` to tell Klipper what MCU the sensor was located on.

```yaml
[temperature_sensor EBB36_Toolhead]
sensor_type: temperature_mcu
sensor_mcu: EBB36_Toolhead
min_temp: 0
max_temp: 100
```

I perviously set up the Raspberry Pi host as an MCU, that needed to be defined as well along with a temperature sensor for it as the host. The host serial path should be the same regardless of machine or installation.

```yaml
[mcu Raspberry_Pi]
serial: /tmp/klipper_host_mcu

[temperature_sensor Raspberry_Pi]
sensor_type: temperature_host
min_temp: 0
max_temp: 100
```

{: .note }
:pencil2: The Pi has an integrated temperature sensor but not all host MCUs do.

Finally, I added the `[exlcude_object]` feature. This is also where I place any included config files.

```yaml
[exclude_object]
[include mainsail.cfg]
```

A `Save & Restart` of the firmware should bring Mainsail back online with the above defined temperature sensors now visible on the frontend.

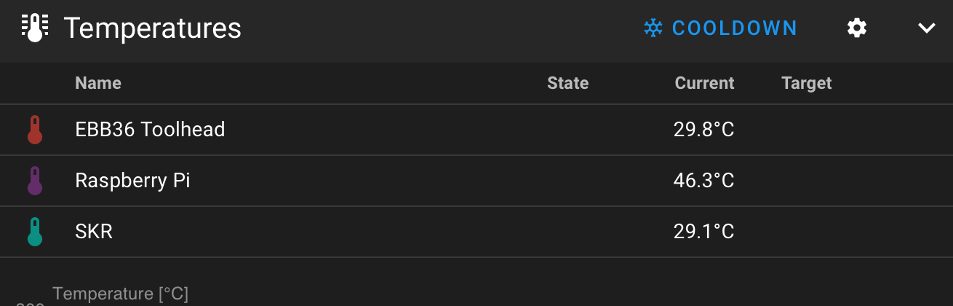
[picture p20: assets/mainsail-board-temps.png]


# Motion

This section contains the printer kinematics, stepper motor configurations, and other motion related settings.

To start, the `[printer]` section needs to be updated. The Ender 3 NG uses corexy kinematics. The accelerations and velocities should also be set but can be tuned later. I started with the following settings:

```yaml
[printer]
kinematics: corexy
max_velocity: 200
max_accel: 2000
max_z_velocity: 5
max_z_accel: 100
```

If a firmware restart is done at this point, an error regarding "step_pin" will appear. This is expected as we have yet to define any stepper motors. Therefore, I next defined the stepper motor configurations.

## Stepper X/Y/Z
{: .no_toc }

The stepper X/Y/Z settings can be pulled off of the [generic BTT SKR Mini E3 v3 config](https://github.com/Klipper3d/klipper/blob/master/config/generic-bigtreetech-skr-mini-e3-v3.0.cfg) with some minimal modifications. Remember, this board uses TMC2209 drivers, so both sections are needed for each motor.

The `step`, `dir`, `enable`, `uart`, and `tx` pins should all be the same. I added comments in the code below to denote what was changed from the generic config.

### Stepper X (A Motor)
{: .no_toc }

Additional configuration settings have been added for sensorless homing.

```yaml
[stepper_x]
step_pin: PB13
dir_pin: !PB12
enable_pin: !PB14
microsteps: 32 #Increased from 16
rotation_distance: 40
endstop_pin: tmc2209_stepper_x: virtual_endstop #For sensorless homing. Also requires DIAG jumper. Hardware pin was ^PC0 
position_endstop: 235 #Set to theoretical max and will be tuned.
position_min: 0 #Added for visibility and will be tuned.
position_max: 235 # Theoretical max. Will be tuned.
homing_speed: 25 #Decreased from 50.
homing_retract_dist: 0 #Disables second homing attempt. Must be disabled for sensorless homing.

[tmc2209 stepper_x]
uart_pin: PC11
tx_pin: PC10
uart_address: 0
interpolate: False #Disable interpolation
run_current: 0.7 # Default 0.580 | Calculated as 70% max_run_current where max_run_current=(rated_current * 0.707). For StepperOnline 17HS15-1504S-X1 motor ((1.50 * 0.707)*0.70=0.742).
stealthchop_threshold: 0 #Use spreadCycle. Default is 999999 for stealthChop
diag_pin: ^PC0 #Jumped endstop pin required for sensorless homing
driver_SGTHRS: 255 #Added at max sensitivity. Must be tuned for sensorless homing
```

### Stepper Y (B Motor)
{: .no_toc }

The `stepper_y` includes most of the same changes as `stepper_x` however I elected to use a physical endstop for this axis.

```yaml
[stepper_y]
step_pin: PB10
dir_pin: !PB2
enable_pin: !PB11
microsteps: 32 #Increased from 16
rotation_distance: 40
endstop_pin: ^PC1 
position_endstop: 235 #Set to theoretical max and will be tuned.
position_min: 0 #Added for visibility and will be tuned.
position_max: 235
homing_speed: 25 #Decreased from 50.

[tmc2209 stepper_y]
uart_pin: PC11
tx_pin: PC10
uart_address: 2
interpolate: False #Disable interpolation
run_current: 0.7 # Default 0.580 | Calculated as 70% max_run_current where max_run_current=(rated_current * 0.707). For StepperOnline 17HS15-1504S-X1 motor ((1.50 * 0.707)*0.70=0.742).
stealthchop_threshold: 0 #Use spreadCycle. Default is 999999 for stealthChop
```

### Stepper Z
{: .no_toc }

The Z axis does not and should not use sensorless homing. My build currently uses a CR Touch and as such this section is immediately followed up by a `[bltouch]` configuration. The base config is outlined below with changes in the comments.

```yaml
[stepper_z]
step_pin: PB0
dir_pin: PC5
enable_pin: !PB1
microsteps: 16
rotation_distance: 8
gear_ratio: 42:20 #Add the 42 tooth printed pulley to 20T motor pulley ratio
endstop_pin: probe: z_virtual_endstop # For CR/BL Touch. Hardware endstop pin was ^PC2
#position_endstop: 0.0 Remove this since a probe is used
position_max: 245 #Set to theoretical max and will be tuned.
position_min: 0 #Added for visibility and will be tuned.

[tmc2209 stepper_z]
uart_pin: PC11
tx_pin: PC10
uart_address: 1
run_current: 0.7 # Default 0.580 | Calculated as 70% max_run_current where max_run_current=(rated_current * 0.707). For StepperOnline 17HS15-1504S-X1 motor ((1.50 * 0.707)*0.70=0.742).
stealthchop_threshold: 0 #Use spreadCycle. Default is 999999 for stealthChop
```

If the firmware is saved and restarted now an error regarding `probe` should appear. Again, this is an expected error as the probe still needs to be configured.

#### Probe
{: .no_toc }

I've included the probe or `[bltouch]` configuration next. It is required in the case a probe is being used as the Z endstop.

{: .notice }
:loudspeaker: Verify the probe and board pins. My installation has the CR Touch connected to the endstop connector on the EBB36 and **NOT** the standard probe pins.

```yaml
[bltouch]
sensor_pin: ^EBB36_Toolhead: PB7
control_pin: EBB36_Toolhead: PB6
y_offset: -18 #Measured per printer/mount. `x_offset` can also be specified.
z_offset: 0 # Required initially but will be tuned.
```

Addtional features of the probe are discussed [here].

At this point, all of the motion components have been defined. A `Save & Restart` should bring Klipper back online with no errors and some motion control available on the front end.

> I suggest completing some [basic motion checks and tuning](/software_config-printercfg-start_tune.html#motion-system) before continuing to build the configuration.

# Extruder

This section defines the extruder motor, heater, and limits. Recall, my build uses an EBB36 toolhead board so all of the pin definitions are in relation to that. Additionally, some configurations were modified for use with the Stealthbuner. Things like PID control and rotation distance will need to be tuned on a per machine basis. Also, rather than specify pressure advance, I use slicer macros to push the value on a per filament basis.

```yaml
[extruder]
step_pin: EBB36_Toolhead: PD0
dir_pin: EBB36_Toolhead: PD1
enable_pin: !EBB36_Toolhead: PD2                                 
rotation_distance: 22.23 #Default value. Will be tuned.
gear_ratio: 50:10 #Stealthburner/CW2 ratio
microsteps: 32
nozzle_diameter: 0.4
filament_diameter: 1.750
heater_pin: EBB36_Toolhead: PB13
sensor_type: Generic 3950
sensor_pin: EBB36_Toolhead: PA3
control: pid # Generic PID settings. Will be tuned.
pid_Kp: 21.527
pid_Ki: 1.063
pid_Kd: 108.982
min_temp: 0
max_temp: 285
max_extrude_only_distance: 101 

[tmc2209 extruder]
uart_pin: EBB36_Toolhead: PA15
interpolate: False
run_current: 0.6
sense_resistor: 0.110
stealthchop_threshold: 0 #Set to 0 for spreadcycle, avoid using stealthchop on extruder
```

If everything is correctly defined, the extruder temperature should now be visible on the Mainsail frontend.

{: .notice }
:loudspeaker: Make sure the extruder temperature is holding steady and not heating. If it is heating, then shut down the printer and start troubleshooting the wiring and/or config definitions.

Other error messages are usually fairly detailed and can assist if issues arise.

I've also included the configuration for the toolhead fans in this section. It made sense to me as they are needed for proper extruder operation.

```yaml
[fan]
pin: EBB36_Toolhead: PA1

[heater_fan hotend_fan]
pin: EBB36_Toolhead: PA0
heater: extruder
heater_temp: 50.0
```

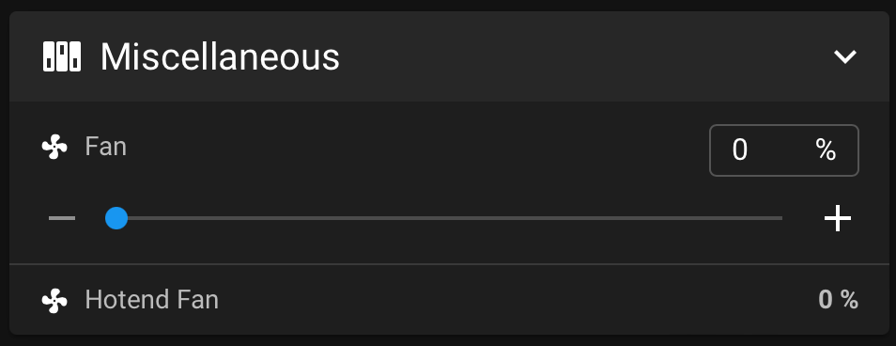
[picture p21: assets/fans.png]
{: .float-right}{: .ml-3}

Once the fans are defined they should also appear on Mainsail. 

> I recommended [verifying the extruder](/software_config-printercfg-start_tune.html#extruder-checks) functions at this stage.

# Bed Heater

Similar to the extruder section the heated bed needs to be defined.

```yaml
[heater_bed]
heater_pin: PC9
sensor_type: ATC Semitec 104GT-2
sensor_pin: PC4
min_temp: 0
max_temp: 130
control: pid # Generic PID settings. Will be tuned.
pid_Kp: 21.527
pid_Ki: 1.063
pid_Kd: 108.982
```

Once again, heater bed should now be visible on the front end with a steady temperature.

> The [heated bed function should be verified](/software_config-printercfg-start_tune.html#verify-heated-bed).

<br>

The basic *printer.cfg* has been built. Before starting to print, some [minimal checks and startup tuning](/software_config-printercfg-start_tune.html#startup-checks-and-tuning) is required if it has not already been done.

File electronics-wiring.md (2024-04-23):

--- 
title: Mainboard Wiring
layout: default
parent: Electronics
nav_order: 1
posted: 2024-04-22
---

# Mainboard Wiring
{: .no_toc }

<details closed markdown="block">
  <summary>
    Table of contents
  </summary>
  {: .text-delta }
1. TOC
{:toc}
</details>

---

The BTT GitHub provides a pinout and schematics of the [SKR Mini E3 v3](https://github.com/bigtreetech/BIGTREETECH-SKR-mini-E3/tree/master). I have included a copy of the pinout for reference. Using this diagram, wiring the board is pretty straight forward. Make sure to use the correct pinout for the mainboard in use.

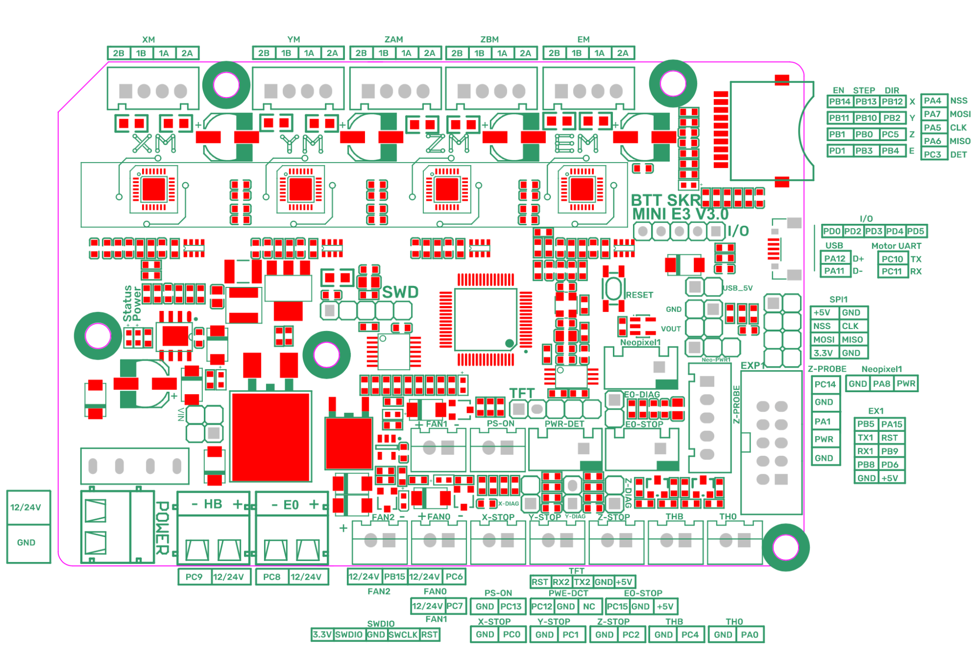
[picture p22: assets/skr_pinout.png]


{: .tip }
:bulb: Pay attention to the pin names using during wiring. Example: `PC9` on the `HB` terminal for the heated bed. These pin names are used in the firmware to control the components.

I've attempted to cover the general wiring of this board in the following paragraphs.

> Sections marked with ":electric_plug:" are either specific to or will change based on the use of CANbus and a toolhead board.

## Power

I wired the 24v power supply directly to the `24v` and `GND` terminals labeled `POWER` on the mainboard. Pay close attention to polarity.

## Heated Bed

The bed heater was also directly wired to the `HB` terminal using ferrules and the same wire from the stock Ender 3 bed. The polarity of the bed is not important. In the future, I would like to add a quick disconnect system at the bed side.

The bed therminstor was also wired directly to `THB` using the original wiring. I did shorten the cable and crimp a new JST connector to the end. Once again, polarity does not matter and I plan to add a disconnect at the bed side.

## Extruder :electric_plug:

The extruder heater and thermistor are wired the same as the heated bed but use `E0` and `TH0`. 

## Fans :electric_plug:

Fans can be wired to any of the 3 JST terminals. Make sure the polarity is correct and the pin name is noted. 

{: .tip }
:bulb: If using the stock Ender 3 hotend blower fan with the blue/yellow wires, blue is `GND` and yellow is `24 VIN`.

## Endstops

Endstops can be wired to their respective location using a JST connector. Polarity is not as important as it can be corrected in the firmware.

### Sensorless Homing

If using sensorless homing, no endstop will be plugged in but rather the `DIAG` pins will need to be jumped. 

## Neopixel

LEDs can be plugged into the `Neopixel1` port in accordance to the pinout for control in the firmware.

## Z-Probe :electric_plug:

The CR and BL Touch probe should be a drop in fit for the SKR Mini E3 v3. However, verify the pinout for all probes prior to connecting.

## EXP1 Header

The stock Ender 3 display cable can be used here to power the stock digital style display with Klipper. The color LCD displays do not work out of the box.

### CAN Tranciver :electric_plug:

The EXP1 header exposes pins `PB8` and `PB9` which are the easiest to access for CANbus. I'm running the SKR Mini E3 in USB to CAN bridge mode so I built a custom 2x3 DuPont connector to utilize `PB8`, `PB9`, `+5V`, & `GND` and connect to a SN65HVD230 CAN tranciver. The table below shows the corresponding EXP1 pins and CAN tranciever pins.

| EXP1 | CAN  |
|---|---|
| +5V  | 3.3V | 
| GND  | GND  |
| PB8  | RX |
| PB9  | TX | 

## USB

It's a MicroUSB port to plug in the Raspberry Pi... The included USB cable should be sufficient.

## Stepper Motors

If using the stock Ender 3 motors and stock wiring harness the motors should pretty much be plug and play. If this is not the case, the motor windings need to be identified. The BTT SKR Mini E3 v3 expects one motor winding on the first two pins of the connector and the other winding to be on the last two pins.

Use a multimeter to find the two motor pins with continuity. This can be identified as winding A which means the remaining two pins make up winding B. Crimp a 4 pin JST connector so the first two pins are one of the windings and the second 2 pins are the other winding. The exact location of each wire/winding is not as important since it can be corrected in the firmware.

### E & Z Motors :electric_plug:

The extruder and Z axis motors can be plugged into their respective connectors. `EM` for the extruder and `ZAM` for the Z axis. 

{: .note }
:pencil2: I believe `ZBM` would work as well since it is the same motor driver and pinout. My understanding is it allows for a second Z motor to be controlled on the same driver.

### A/B Motors

I plugged the A motor, left side motor if looking at the E3NG head on, into `XM`. That leaves `YM` for the B Motor. I'm not 100% sure if that is the correct way but it works so I have no complaints.

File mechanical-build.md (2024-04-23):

---
title: "Mechanical Assembly"
layout: default
nav_order: 5
posted: 2024-04-10
updated: 2024-04-22
---

# Mechanical Assembly
{: .no_toc }

<details closed markdown="block">
  <summary>
    Table of contents
  </summary>
  {: .text-delta }
1. TOC
{:toc}
</details>

---

The order of steps presented here is how I built my machine. This should not serve as a replacement for the official build manual but rather a supplement. The assembly of the parts is still the same I just reorganized some things and added a few others. I attempted to highlight things that are unique to my build, including the official mods that may not be completely outlined in the manual.

See [Preparing Parts](/preparing.html) for some of the things I did before actually starting the mechanical build.

# A/B Stepper Motor Mounts

Nothing special here. I just followed the build instructions exactly as written.

# Y Gantry

After building these, make sure to keep the M5x50 screws loose enough that the linear rods will fit into the openings. Additionally, I found my tolerance pretty tight on this parts. The LM8LUU bearing snapped in but I needed to bore out the 8mm holes for the rods. :us: A 5/16" drill is 7.94mm. A little sung but it worked.

Additionally, the races of the bearings should be offset 45&deg; in relation to gravity. This helps ensure best performance, smooth operation, and even wear. See the image beloew for reference.

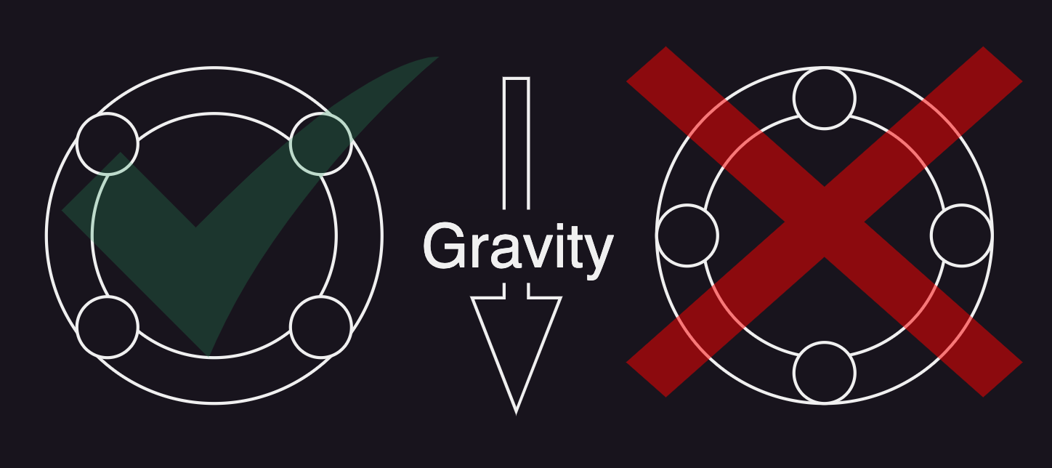
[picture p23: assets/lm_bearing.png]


{: .tip }
:bulb: Don't forget to lubricate the bearings prior to installation.

# Toolhead

Since I am not using the stock toolhead, I only built the back half of this assembly. That meant using `XC0`, `XC1`, & `XCB` along with the LM8LUU bearings and appropriate screws. On second thought, I could have use the appropriate mount plate `XC1` for my toolhead of choice right from the start. 

{: .tip }
:bulb: There is enough room to change out this part and the toolhead after it has been mounted on the printer.

{: .mod }
:wrench: I'm using a standard [Voron Stealthburner](https://vorondesign.com/voron_stealthburner) toolhead along with this [remixed `XC1` plate](https://www.printables.com/model/709806-ender-3-ng-vocano-voron-bltouch-stealthburner). I also modified my CR touch to fit.

# Belt Tensioners

I found the bearings to fit fairly sung in my printed pulleys. I used `BT1` & `BT2` without the external washers to press fit the F695 bearings in place. Once they were fitted, I put the external washers back in place.

# Z Axis Belt Tensioner

I built this in accordance to the manual except for the spring. I didn't have any extra bed springs so I used the old Ender 3 extruder spring.

# Bottom Frame

I built each of the frame pieces then attached them to the bottom frame extrusions as I went. Leadscrews were installed last.

## Front Corners

These parts require the Z belt be installed prior to capping them off with `BLFB` & `BRFB`. Make sure the belt isn't twisted or tangled. Don't over tighten the screws holding on the rubber feet as they may just punch through the mount holes on the feet. I used additional washers to help increase the surface area. I held off on installing the leadscrew for now. At this point, I mounted the front corners to the donor 4040 and 2020 extrusions that will form the base of the printer

## Rear Corners

I didn't want to fight with printing the large vertical beams so I used the 350mm 2040 extrusion mod which required the use of `BLR_2040_350` and `BRR_2040_350`. These bolted directly onto the bottom frames X/Y extrusions with M5x12s. I also secured them to the rear 4040 extrusion.

## Z Axis Support and Stepper

My build uses the 1040mm Z belt and needed `BZA_1040`. Its essentially a combination of the Z stepper mount and leadscrew mount. The assembly is similar enough. However once again, it requires the Z belt to be routed prior to completing the assembly of this part so make sure the belt has no twists and follows the correct path.

## Completing Bottom Frame Assembly

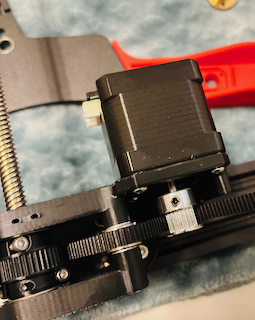
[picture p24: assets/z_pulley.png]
{: .float-right}{: .ml-3}

At this point, the bottom frame has been assembled with each corner bracket. The rear Z support still needs to be attached, leadscrews inserted, and belt tensioned. I attached `BZA` to the rear extrusion using the T nuts. I bolted the Z tensioner to the right extrusion. While the Z belt was still loose, I inserted each of the 3 three lead screws. When installing the lead screws, make sure they go through both 608 bearings but not so far that it hits the surface below. Secure the lead screws using the grub screws on the three Z pulleys. The Z motor pulley may need to be adjusted so it is level with the screw pulleys. I waited until the mounting the bed before I tensioned and secured the Z belt to each pulley.

Finally, I went ahead and slid the vertical 350mm 2040 extrusions in place and secured them with T nuts. I also screwed the rear rubber feet into holes I tapped on the bottom of these extrusions.

# Bed Assembly

I assembled the bed using the stock plate. Use care when tightening the screws that hold the LM12UU bearings. `ZCL` is easy to crack. I reused the lead screw nut from the Ender 3. It was not an exact match to the mounting pattern on the printed arms. As a result, I needed use some M2 bolts and a nut to secure it. I will be replacing this particular nut.

## Mounting the Bed Assembly

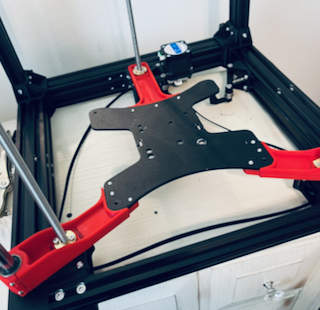
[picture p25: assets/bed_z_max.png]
{: .float-right}{: .ml-3}

Start by inserting the 12mm linear rods into the bottom frame. Then line up the left and right sides of the bed frame with the lead screws and rods. Next, I slid the Z motor assembly until the rear lead screw was in the correct position and secured the assembly. I alternated turning each lead screw until the bed frame assembly was in the lowest possible position on each arm. I knew for a fact, this would be the lowest point the bed can move. I now routed the Z belt over each pulley and applied tension with the Z tensioner. Now, by turning one screw, I was able to move the bed assembly up and down equally on all 3 screws.

{: .tip }
:bulb: Apply a little grease to the lead screws during this process to keep them clean and running smooth.

Follow the manual's instructions on aligning the bed carriage if the screws don't sit in the middle of the anti wobble mounts.

## Mounting the Build Plate

The stock build plate can be placed over the stock mounting holes. I used my existing bed springs since they were already the yellow ones. I also used the old adjustment wheels. Make sure to use the printed spacer for the front wheels and the rear cable strain relief.

# Top Frame Assembly

All of the X/Y components have already been assembled, now I put them together and mounted the top frame. Per the manual, I secured the 2020 top rear extrusion and 2040 top side extrusions to the A/B motor mounts. Rather than install the X/Y axis assembly as one piece, I first inserted the 8mm linear rods into the A/B mounts. Next, I assembled the X gantry with the 2x linear rods, toolhead assembly, and 2x Y ends. This gave me the ability to easily adjust the length so the Y gantry ends fit the top frame without binding. 

I now mounted the top front corners and placed the entire top assembly on the lower frame. Since I used the 2040 mod, I needed to secure the rear top corners with `TJL-2040` & `TJR_2040`.

# Square and Secure

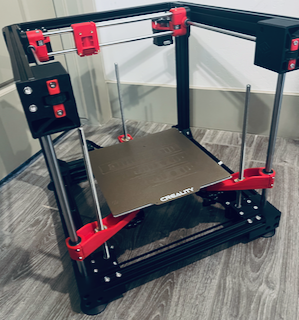
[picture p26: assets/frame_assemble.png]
{: .float-right}{: .ml-3}

Check each corner of the frame for a square assembly. I used a speed square along with a solid flat surface. Make sure to tighten the bolts securing each corner bracket. Tighten the set screws on the top and bottom front joints that hold the 12mm rods in place. Move the X, Y, & Z axes for their full range of motion to check for binding. Make adjustments as needed.

I also added the top `FCB2` and bottom `FCB1` frame corner braces at this time.

# AB Belt Routing

I routed the A/B belts prior to installing the electronics panels. Partly because it gave me more room and partly because I was waiting on some hardware. Follow the steps in the build manual with a few very important caveats.

1. Make sure to leave plenty of excess at each end of the belt. About 5cm is probably a good number.
2. Don't miss the idler that is hidden behind the A/B motors. Its not really visible on from the outside and hard to see on the drawings. Refer back to the A/B Mount building instructions to see it clearly.
3. Align the motor pulley with the center of the belt path.

# Electronics Panels

Not much to add here. The 2040 mod requires the use of additional T nuts to mount the panels and a shorter DIN rail. I screwed the DIN rails directly to the electronics panels. I would like to find a way to better secure the lower, longer DIN rail as it seems to put a lot of stress on these panels.

# Extras

STLs for a spool holder and handles are included in the release files. I will be adding those once I am further along in the build. I feel as if they will be in the way during the wiring phase.

# Completion

Give the build a final inspection. Check for cracks or damaged parts. Make sure the joints and mounts are secure. Check that their is still no binding and each axis has a full range of motion. Now is the easiest time to address any issues or replace any parts. I also took this opportunity to mount the toolhead.

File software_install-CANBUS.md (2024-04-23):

---
title: "CANbus Software Installation"
layout: default
nav_order: 2
parent: "Software Installation"
posted: 2024-04-15
updated: 2024-04-22
---

# CANbus Software Installation
{: .no_toc }

<details closed markdown="block">
  <summary>
    Table of contents
  </summary>
  {: .text-delta }
1. TOC
{:toc}
</details>

---

{: .notice }
:loudspeaker: This is considered an advance configuration and assumes some underlying knowledge of Linux/Raspberry Pi OS and Klipper.

> Special thanks to [Esoterical's CANBUS Guide](https://canbus.esoterical.online) and [Zippy's CANBus Your Pico](https://github.com/rootiest/zippy_guides/blob/main/guides/pico_can.md).

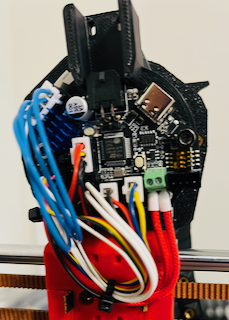
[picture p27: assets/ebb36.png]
{: .float-right}{: .ml-3}

CANbus is communication protocol that only uses 2 wires. Most commonly in 3D printers it is used to connect a second MCU, often a toolhead board, to the main controller. This is exactly the use case I have set up. I am running a [BTT EBB36](https://github.com/bigtreetech/EBB) mounted on my toolhead. All of the toolhead electronics (hotend, thermistor, fans, LEDs, extruder motor, bed probe, etc.) are connected to that board. The board is then connected to my main MCU using 2 wires and a CAN transceiver. The board does also require 2 wires for power. So now all of my toolhead electronics and managed using only 4 wires back to my electronics case.

> It is worth noting the EBB36 can be connected in USB mode and does not require the use of CANbus. Additionally, other boards are available and there are some other ways to run CANbus on a 3D printer. This covers using a BTT SKR Mini E3 V3 as a USB to CAN bridge along with a cheap CAN transceiver to communicate with the EBB36. Klipper then connects to all of these devices using CAN rather than USB.

{: .notice }
:loudspeaker: All of the CAN devices must be correctly wired and powered for this to work. See the section on [electonics & wiring](/electronics.html) for inspiration.

# Build the CAN Network

For Raspberry Pi OS set up the CAN interface with:

```console
sudo nano /etc/network/interfaces.d/can0
```

Then populate the file with the following block:

```yaml
allow-hotplug can0
iface can0 can static
  bitrate 1000000
  up ip link set can0 txqueuelen 1024
```

This sets up the CAN network with a bit rate of 1,000,000 as recommended in the Klipper docs and a transmit queue length of 1024. The Klipper docs recommended 128. Other guides recommended higher. After struggling with `timer too close` errors, I found 1024 works well.

Once these are saved, reboot the Pi.

# Flash the BTT SKR Mini E3 V3

{: .notice }
:loudspeaker: These steps are specific to the BTT SKR Mini E3 v3 mainboard. It will need to be adapted for any other device.

Make sure some python dependencies are installed on the Pi:

```console
sudo apt install python3 python3-pip python3-can
```

## Build & Flash Katapult

I elected to install [Katapult](https://github.com/Arksine/katapult) on the SKR. This allows the CANbus network to be used to flash Klipper firmware. Normally, the SKR Mini E3 v3 must be flashed directly from the SD card slot. Katapult replaces the default bootloader to make this possible. However Katapult is not mandatory for CANbus. Skip ahead to [building and flashing Klipper](/software_install-CANBUS.html#build--flash-klipper) to manually flash firmware without Katapult.

{: .warn }
:warning: Overwriting the bootloader on the SKR Mini E3 V3 has the potential to brick the mainboard if done incorrectly. Proceed with caution.

Start by cloning [Katapult](https://github.com/Arksine/katapult) to the Pi.

```console
cd ~
git clone https://github.com/Arksine/katapult
```

Open the configuration tool and begin to configure the firmware.

```console
cd ~/katapult
make menuconfig
```

I have included a screenshot of the relevant settings. Once again, remember this is specific to the **BTT SKR Mini E3 V3**.

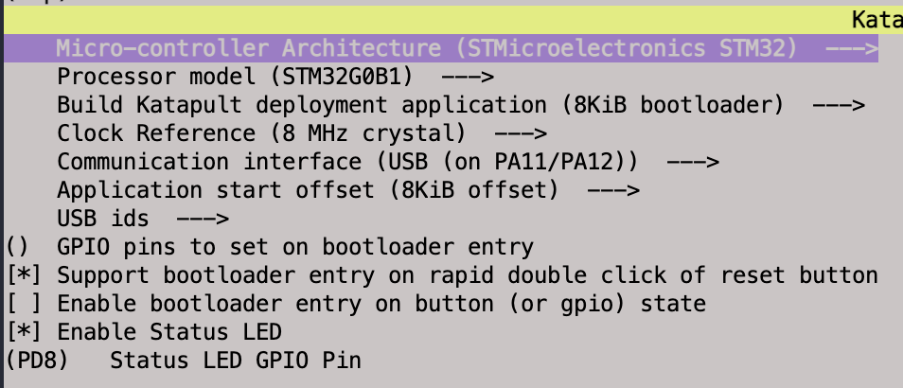
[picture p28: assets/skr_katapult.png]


Build save the configuration and build the new firmware/bootloader.

```console
make clean
make
```

The new bootloader will have been generated as `deployer.bin` under the path `~/katapult/out/deployer.bin`.

The bootloader must be installed from the SD card slot. Copy `deployer.bin` to a MicroSD card that has been formatted to FAT32. Rename `deployer.bin` to `firmware.bin`.

Power off the printer mainboard, insert the firmware SD card, and power on the mainbaord. Wait several moments for the new bootloader to flash.

Assuming it was all done in accordance with the above screenshot, the status LED should start to slowly blink indicating Katapult mode.

Additionally, running `ls /dev/serial/by-id` should show a Katapult device connected via USB.

```console
usb-katapult_stm36g0b1_########-####
```

Make note of the above device name as it will be needed to flash Klipper later.

## Build & Flash Klipper

Klipper needs to be built for the SKR Mini E3 v3 to communicate via CANbus. Open the Klipper configuration tool.

```console
cd ~/klipper
make menuconfig
```

Build the configuration for the BTT SKR Mini E3 v3 to communicate via `USB to CAN`. Make sure the bootloader offset is agrees with the Katapult install. Select a CANbus interface, `PB8/PB9` are pins easily accessible on the EXP1 header. Finally make sure the bit rate is the same as the previously configured CAN network. Once again, I have attached a screenshot of my configuration for a BTT SKR Mini E3 v3 for CANbus in bridge mode with Katapult.

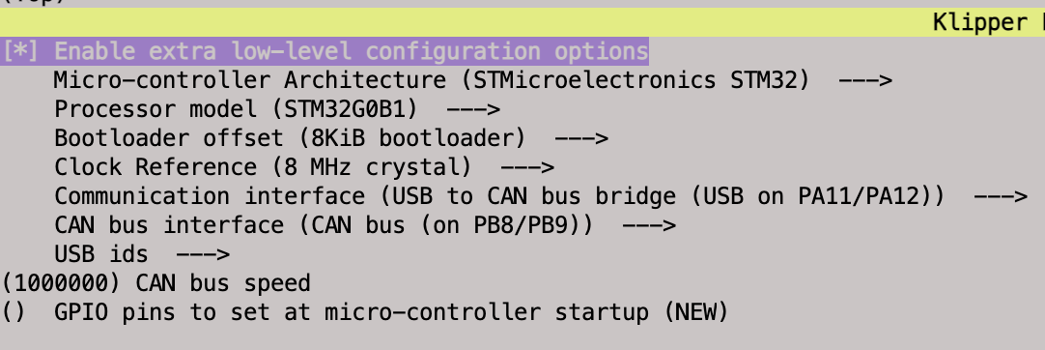
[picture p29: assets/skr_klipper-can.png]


Save the configuration and generate the firmware.

```console
make clean
make
```

This will generate the firmware as a `klipper.bin` file in under the standard path of `~/klipper/out/klipper.bin`. It is now ready to be flashed [with Katapult](/software_install-CANBUS.html#flash-with-katapult) or [without Katapult](/software_install-CANBUS.html#flash-without-katapult).

### Flash without Katapult

If not using Katapult, the new firmware must be flashed via SD card. Copy `klipper.bin` to a MicroSD card that has been formatted to FAT32. Rename `klipper.bin` to `firmware.bin`.

Power off the printer mainboard, insert the firmware SD card, and power on the mainbaord. Wait several moments for the firmware to flash.

### Flashing with Katapult

If Katapult is installed on the mainboard, the Klipper firmware can be flashed directly without the need for an SD card. 

First stop the Klipper service.

```console
sudo service klipper stop
```

Navigate to and run the Katapult flash script:

```console
cd ~/katapult/scripts
python3 flashtool.py -d /dev/serial/by-id/usb-katapult_stm36g0b1_########-####
```

{: .tip }
:bulb: Make sure to use the correct `/dev/serial/by-id/` path for the Katapult mainboard as found when it was [previously flashed](/software_install-CANBUS.html#build--flash-katapult).

## Connect via CAN

The CAN network should now be running. Assuming the network is `can0`, This can be verified with:

```console
ip -s -d link show can0
```

The output should show the details of the CAN network, including the bit rate and transmit queue length set previously.

The mainboard should also be visible as a CAN device with `lsusb`.

The CANbus query tool will discover the CANbus UUID of the mainboard.

```console
~/klippy-env/bin/python ~/klipper/scripts/canbus_query.py can0
```

This UUID will be used in the `printer.cfg` file to tell Klipper to use CAN for communication. Remove the `serial` line and add the `canbus_uuid` as it corresponds to your machine.

```diff
[mcu]
- serial: /dev/serial/by-id/usb-Klipper_Klipper_firmware_12345-if00
+ canbus_uuid: 027a9447a345
```

Assuming everything went according to plan. The Mainsail interface should now be accessible without any `mcu` communication errors and via CANbus.

# Flash the BTT EBB36 Toolhead Board

The whole reason I set this up it to use the EBB36 via CANbus. Now that board needs to be flashed with Klipper and setup as an additional MCU with CANbus communications.

{: .notice }
:loudspeaker: These steps outline how I setup my BTT EBB36 v1.2 board. They will vary between board models and versions. Adjust as needed.

## Build & Flash Katapult

The host should already have Katapult cloned from the previous steps. Now Katapult must be built and flashed to the EBB36 to allow Klipper to be flashed and updated via CAN.

```console
cd ~/katapult
make menuconfig
```

Select the settings as they apply to the specific board being used make sure to use the same speed and offsets as all other devices on the CAN network. Once again, I have included a screen shot of the settings I used specific to my BTT EBB36 v1.2.

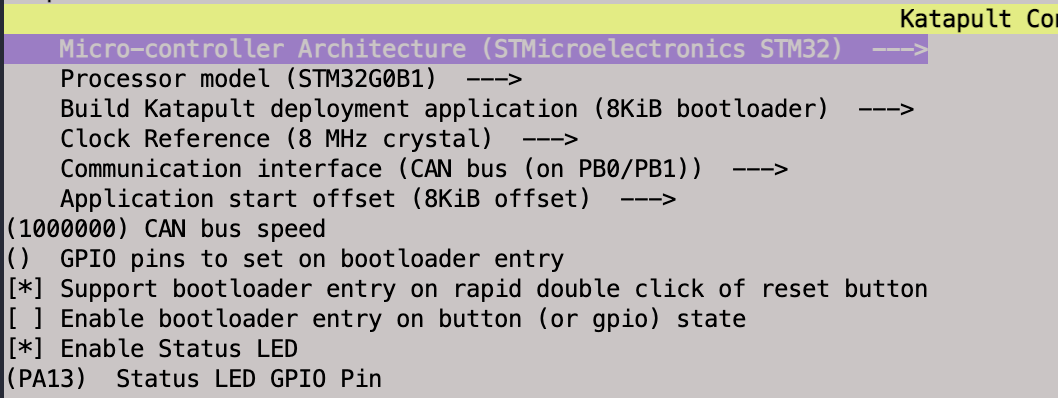
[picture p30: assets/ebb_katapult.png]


Save then build the firmware file.

```console
make clean
make
```

Now the board needs to be powered and connected to the Raspberry Pi host via USB. If the board already has a 24v power source connected, then all that needs to be done is plug a USB data cable into the board and Pi. 

If the board has not yet been wired to a 24v power source, it can temporary be powered via USB by placing a jumper across the VUSB pins as shown below.

{: .warn }
:warning: Do not jump these pins if the board has a 24v power supply attached as it can result in damage to the components.

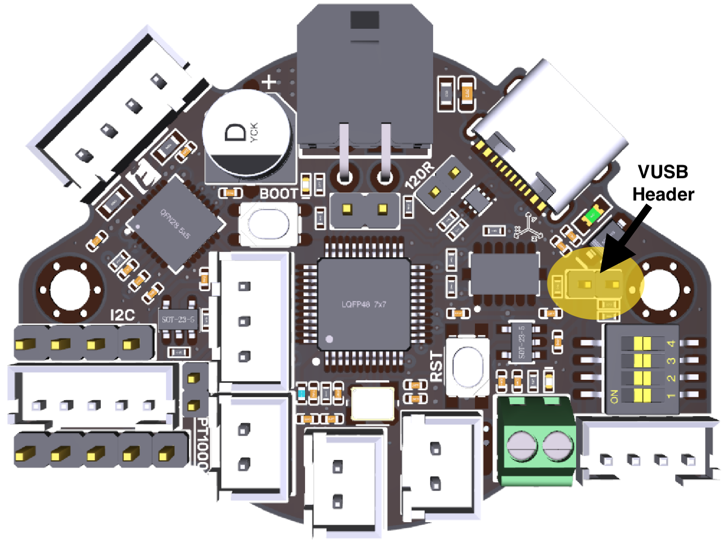
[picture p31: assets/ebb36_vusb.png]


Next place the board in device firmware upgrade (DFU) mode by holding the `boot` button and pressing `rst`. 

{: .warn }
:warning: Use caution when in DFU mode if a heater is connected to the board. I have heard reports of the heaters being powered while in DFU mode.

Verify the board booted into DFU mode and is attached to to the Pi:

```console
sudo dfu-util -l
```

Make sure to grab the device ID (####:df##) and internal flash address (0x0#####). Use these values to flash Katapult onto the EBB36.

```console
sudo dfu-util -R -a 0 -s 0x0####:force:mass-erase:leave -D ~/katapult/out/katapult.bin -d ####:df##
```

After the process is complete `File downloaded successfully` should display along with `dfu-util: Error during download get_status`. Ignore the error then shutdown the Pi and printer.

Remove the USB cable and any jumpers needed for the flashing. Make sure the EBB has 24v power and is connected via CAN. Power everything back on.

If the `Status LED GPIO Pin` was enabled and set correctly, the EBB LED shoudl be blinking about once per second to indicate it has booted into Katapult.

In order to find the UUID and verify the board is on the CAN network and in Katapult mode, run:

```conole
python3 ~/katapult/scripts/flashtool.py -i can0 -q
```

Record the UUID and make sure it is showing `Application: Katapult`.

## Build and Flash Klipper

Build the Klipper firmware specific to the toolhead board:

```console
cd ~/klipper
make menuconfig
```

Once again pay attention to the bus speed, clock reference, and bootloader settings making sure they agree with the other CAN device settings. Adjust all settings in accordance with the specific toolhead board. A screen shot of my EBB36 v1.2 Klipper settings is below.

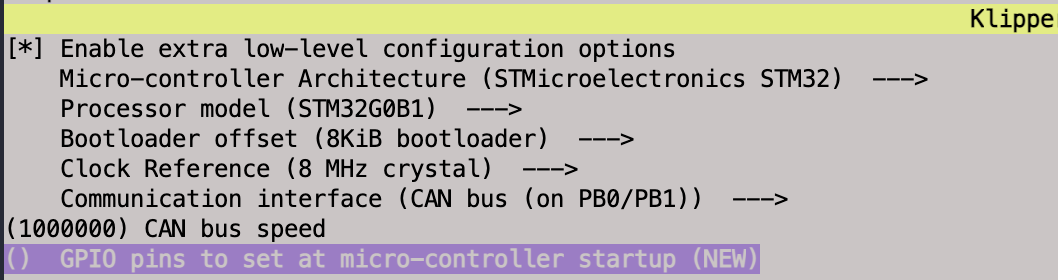
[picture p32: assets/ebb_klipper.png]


With the correct settings, save and build the Klipper firmware.

```console
make clean
make
```

Stop the Klipper service.

```console
sudo service klipper stop
```

And Flash the new Klipper firmware file to the EBB36 via CANbus and Katapult. Make sure to use the UUID recorded after [building and flashing Katapult](/software_install-CANBUS.html#build--flash-katapult-1) on the EBB.

```console
python3 ~/katapult/scripts/flashtool.py -i can0 -u ####UUID### -f ~/klipper/out/klipper.bin
```

Confirm the flash with:

```console
~/klippy-env/bin/python ~/klipper/scripts/canbus_query.py can0
```

A `canbus_uuid` with `Application: Klipper` should be the resulting output. Record this UUID for use in the `printer.cfg` file and restart the Klipper service.

```console
sudo service klipper start
```

## Add the Toolhead MCU

Add the toolhead MCU to `printer.cfg` with the following lines:

```yaml
[mcu EBBCan]
canbus_uuid: 0e####0c
```

Where the `canbus_uuid` is the UUID previously obtained from `~/klippy-env/bin/python ~/klipper/scripts/canbus_query.py can0`. The `EBBCan` is the name of this toolhead MCU and is the default used by BTT. It can be modified if desired.

# Configuration

By now, the BTT SKR Mini E3 v3 and BTT EBB36 v1.2 should be communicating via CAN. The next section covers the [configuration of Klipper](/software_configuration.html) and other software, including the secondary MCU and CAN references.

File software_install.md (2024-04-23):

---
title: "Software Installation"
layout: default
nav_order: 7
has_children: true
posted: 2024-04-15
updated: 2024-04-22
---

# Software Installation
{: .no_toc }

<details closed markdown="block">
  <summary>
    Table of contents
  </summary>
  {: .text-delta }
1. TOC
{:toc}
</details>

---

I already use Klipper with Mainsail on my current printers so it was a natural choice for this project. My installation is running on a Raspberry Pi. Since I prefer to start with a bare bones system and cherry pick what I need, I flashed Raspberry Pi OS Lite then used [KIAUH](https://github.com/dw-0/kiauh) for a "manual" install.

{: .tip }
:bulb: I have a tutorial for [Baking a Raspberry Pi](https://themakermedic.com/posts/Pi-Baking_a_Pi/) in my other blog.

Since so much information already exists between the [KIAUH](https://github.com/dw-0/kiauh) docs along with the [Klipper](https://www.klipper3d.org) and [Mainsail](https://docs.mainsail.xyz) pages I suggest referring to them for more details on the installation process and methods. Here I will outline some basic steps for my general software install and do a deeper dive into things like CANBus and other unique features of my build.

# Klipper Host

The first step is to get a Klipper host up and running. I'm running a bare bones install of Raspberry Pi OS Lite on a Raspberry Pi. Using [KIAUH](https://github.com/dw-0/kiauh), I installed Klipper, Moonraker, and Mainsail. Klipper and Moonraker are mandatory but the frontend, in my case Mainsail, can be different. KIAUH also includes some other software that can be installed at this time if desired. These installations can also be done manually by referencing the individual documentations.

## RPi as an MCU

The Raspberry Pi can also be used as a secondary MCU. This means the GPIO pins on the the Pi can be accessed and controlled by Klipper. Since we're already in the Pi, might as well set that up now.

Open the Klipper directory and set the MCU process to start before Klipper:

```console
cd ~/klipper/
sudo cp ./scripts/klipper-mcu.service /etc/systemd/system/
sudo systemctl enable klipper-mcu.service
```

Build the MCU firmware by running `make menuconfig` and selecting `Linux process`.



Once the firmware is built, flash it to the Raspberry Pi:

```console
sudo service klipper stop
make flash
sudo service klipper start
```

## Sonar

I also run [Sonar](https://github.com/mainsail-crew/sonar) on my build. Its a WiFi keepalive daemon and occasionally my Pi likes to drop connections. They also provide a straight forward install script.

{: .tip }
:bulb: I also found running the Pi on a 2.4 GHz only WiFi and with IPv6 disabled seems to be more stable.

# Mainboard (BTT SKR Mini E3 V3)

{: .mod }
:wrench: I am running my personal setup in a USB to CAN configuration. This this is covered [here](/software_install-CANBUS.html). The steps below outline a basic Klipper install.

The Klipper firmware needs to be compiled and flashed to the mainboard. On the host run the following:

```console
cd ~/klipper
make menuconfig
```

This opens the Klipper configuration tool. Make the selections in accordance with the mainboard in use. The Klipper GitHub contains a list of [example configs](https://github.com/Klipper3d/klipper/tree/master/config) for many mainboards along with the required settings. 

I've provided a screenshot of the standard SKR Mini E3 V3 settings using USB communications.

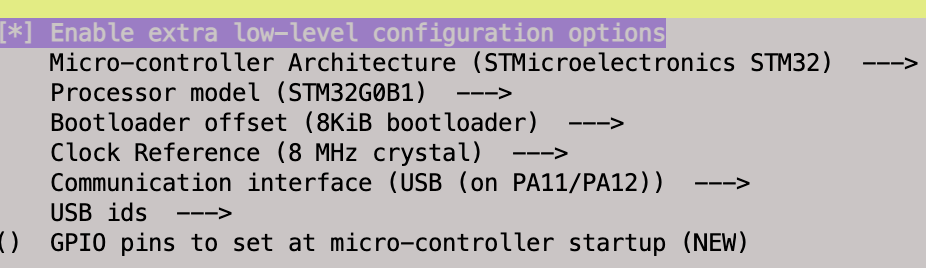
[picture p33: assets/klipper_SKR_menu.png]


After setting and saving the required values clear out any previous firmware builds and generate the new firmware file.

```console
make clean
make
```

This will generate the firmware as a `klipper.bin` file in under the standard path of `~/klipper/out/klipper.bin`

The SKR Mini E3 V3 requires the firmware be flashed via SD card. Copy `klipper.bin` to a MicroSD card that has been formatted to FAT32. Rename `klipper.bin` to `firmware.bin`.

{: .tip }
:bulb: Copy the firmware with whatever method works best. I've used SCP, SFTP, Samba, and a direct mount in the past.

>I've had issues with 32GB Samsung MicroSD cards flashing the firmware. The cheap 8GB card that came with my Ender always works fine though.

Power off the printer mainboard, insert the firmware SD card, and power on the mainbaord. Wait several moments for the firmware to flash.

A successful flash can be confirmed in two ways.

1. Assuming the Pi is connected via USB to the SKR run:
```console
ls /dev/serial/by-id
```
An output similar to `usb-Klipper-stm32g0b1xx_#####################-####` should be generated.

     __*OR*__

2. Insert the SD card back into a computer and the `firmware.bin` file should have automatically changed to `firmware.cur`

Use the `ls /dev/serial/by-id` output in the `printer.cfg` file to tell Klipper where it can find the control board.

```console
[mcu]
serial: /usb-Klipper-stm32g0b1xx_#####################-####
```
With Klipper installed on the Pi and flashed to the mainboard. Its time to start the [configuration](/software_configuration.html).

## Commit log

2024-03-27 Add Ender Printed Parts
2024-05-09 Extras-Serial Plate
